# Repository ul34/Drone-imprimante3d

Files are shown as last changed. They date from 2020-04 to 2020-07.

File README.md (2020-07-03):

# Drone-imprimante3d
P.I.D &amp; I3D

                                               DRONE QUADRIMOTEUR EN X.

 Drone Frame impression 3D 

-Quel type de plastique utiliser ?

Personnellement j'ai utilisé du PETG mais cela est une solution non optimale. Le polypropylène plus difficile à imprimer, ne colle pas aux surfaces de type build-plate ou verre. Le polypropylène ne colle que sur sur le polypropylène. Son désavantage est sa résistance mécanique plus faible à l'étirement que la plupart des plastiques. Il possède néanmoins une grande résistance au choc et une bonne flexibilité. Pour notre projet la résistance au choc est essentielle.

Paramètres impression 3D 

-Surface d'impression minimale pour ce drone 180*180 mm.
-Température impression buse PETG : 245 C°
-Température impression plateau PETG : 80 C°
-Buse 0.6 mm
-Hauteur de couche 0.2 mm
Remarque: les températures d'impression varie en fonction de la marque de plastique utilisée.

Fichier impression 3D 

-Drone.montage.stl ce fichier n'est pas à imprimé, il montre juste l'assemblage des différentes piéces.
-N.basdrone.stl ce fichier contient la pièce du bas du drone avec le support de batterie (lorsque vous imprimerez cette pièce activer les supports).
-N.ruche.stl ce fichier contient la pièce du haut qui permet de fixer les bras du drone.Il faut que les losanges soient perpendiculaires au losange de la pièce du bas pour avoir une rigidité égale.
-N.bras.stl ce fichier permet d'imprimer les bras du drone, dupliquez les au nombres de 4 dans votre slicer (Cura...).
-N.calibras.stl ce fichier permet d'imprimer des pièces alignées au milieu sur la longueur et la largeur du drone. Elle permettra de glisser un rond de 6mm de diamètre pour pouvoir calibrer les coefficients P.I.D des axes PITCH et ROLL.
-N.supMPU6050.stl ce fichier contient l'impression du support gyroscope, imprimez deux support.

Matériel 

-MPU6050 *2 ~5€
-ESC 30A *4 ~20€
-arduino Uno ou arduino Mega
-Radiocommande Flysky fs-i6 avec récepteur ~45€
-Moteur brushless BR2212 1000KV *4 ~20€
-Batterie 3S 11.1v ~30€
-Hélices horaires * 2
-Hélices anti-horaires

Microcontrôleur 

L'Arduino est un circuit électronique composé d'un microcontrôleur que l'on peut appeler micro-ordinateur il possède de la mémoire morte reprogrammable (EPROM), de la mémoire vive et un processeur qui fait les calculs,il est doté d'entrée est de sortie, alors il peut communiquer de l'information sous forme électrique(OUTPUT)est recevoir de l'information(INPUT). Il ya la partie alimentation composée d'un ou de plusieurs régulateur qui va limiter la tension a 5v est 3.3v avec des Condensateur est des résistances qui permettent de stabiliser la tension, un MiCro a besoin d'une alimentation très stable pour fonctionner correctement. il y a aussi l'oscillateur qui permet au MiCro de se repérer dans le temps est déterminé aussi sa rapidité d’exécution en HZ. Puis la dernière partie qui est un convertisseur USB::UART qui vous permet de téléverser le programme dans le MiCro, mais pas que, il permet aussi de recevoir des données pour voir si notre Prog est fonctionnel. Résumons l'arduino est un MiCro "Plug&Play" qui va nous permettre de recevoir des donnés les transformer avec des calculs puis transmettre des données a des composants electronique.
Le gyroscope & accéléromètre 
-Le MPU6050 est une centrale inertielle qui réuni gyroscope et accéléromètre ce qui permet au microcontrôleur de connaître la position du drone autour de trois axe X = ROLL, Y = PITCH, Z = YAW en degrés et la vitesse a laquelle il se déplace en degrés/S. Vous verrez plus tard qu'il est paramétrable cela nous permettra de déterminer une certaines plage de mesure ou activer des filtres. Il communiquera avec l'arduino via le protocole de communication nommé "I2C".

ESC 

-Les ESC sont des circuit électronique composer d'un MiCro avec un programme qui contrôle des transistor Mosfet qui on le rôle d'interrupteur pour pouvoir commuter le courant électrique est changer le sens du champ magnétique des bobines(situées sur le stator) en fonction de la position du rotor constitué d'aimants, cette position est donnée au MiCro via des capteurs a effet Hall ou dans notre situation la force contre électromotrice. Le MiCro peut alors suivre la séquence propre au moteur et le faire tourner, pour contrôler la vitesse de rotation le MiCro utilise le rapport cyclique(PWM) en contrôlant les interrupteurs (Mosfet), pour vous donner un exemple imaginez une led avec un interrupteur que nous allumons 500ms puis éteignons 500ms et ainsi de suite nous avons alors un signal cyclique puis qu'il se répète, on peut aussi déterminer notre période qui est de 1s imaginons maintenant que notre led consomme 1 w/h = 3600 joule soit une consommation en énergie de 1 joule par seconde vu qu'une heure est égale a 3600s donc si notre led est allumée en permanence elle consomme 1 joule/S mais nous ne l'allumons que 50 % du temps donc la led recoit 50% de l'énergie quelle pourrait recevoir par apport au temps exemple sur 1h la led a consommée 1800J a la place de 3600J mais si vous faite cette expérience avec une période aussi longue 1s vous verrez la led clignoter et ce n'est pas le but recherché. L'objectif est de pouvoir moduler la luminosité de la led, pour cela il faut réduire la période pour que l'allumage et l'extinction passe sous le seuil de perception visuelle(~100ms) exemple 10ms allumé 10Ums éteint plus la période diminue plus la fréquence est élever et cela nécessite d'avoir des interrupteur qui peuvent commuter rapidement. Le calcul est le suivant (Rapport cyclique en % = durée allumé / durée période). Maintenant revenons a nos ESC plus la frequence "PWM" est élever plus la régulation de vitesse sera précise est constante, mais il faut alors un ESC avec des transistor de bonne qualité et capable de fonctionner a haute frequence pour notre premier drone se préoccuper de la frequence d'échantillonage n'a pas vraiment d’intérêt puisque nous utilisons des ESC bas de gamme. Malgré ses explication nous ne savons toujour pas comment envoyer de l'information au MiCro des ESC pour qu'il puisse réguler la vitesse mais vous allez voir que ce n'est pas très difficile, c'est notre controleur de vol qui envoie l'information au ESC, nous allons envoyer l'information en controlant la largeur d'impulsion pour étre plus clair c'est le temps que le signaux réste a l'état haut(5v) a ce niveau la frequence n'est pas trés importante pour notre cas. En général la longueur d'impulsion varie entre 1000us ce qui signifie moteur a l'arrét est 2000us qui correspond au moteur a pleine puissancece ce qui fait "théoriquement" 1000 vitesse différente possible.

- Moteur brushless

-Ce sont des moteur électrique sans balais est collecteur car ses moteur peuvent avoir une vitesse de rotation trés élever ce qui augmente la durée de vie du moteur mais il faut en contrepartie un circuit electronique pour assurer le role des balais est collecteur, l'orsque vous acheté des moteurs de drone vous verrez des inscriptions il ya d'abord les dimensions du moteur puis une indication sur la vitesse de rotation en fonction du voltage, je vais vous donner un exemple "BR2212 1000KV" vous voyez le nombre 2212, composé de quatre chifre ?. Les deux premier chiffre "22" indique le diamétre du stator et les deux suivant représente la hauteur du stator "12". Les KV vous donnent la vitesse du moteur en fonction du voltage que vous lui donné, nous avons la un moteur "1000KV" si je lui donne 2V le moteur tournera alors a 2000 tour/minutes. Nous allons maintenant parler du fonctionnement d'un moteur brushless tout d'abord il existe deux variantes le Brushless in-runner ou le stator est en périphérie est le rotor est central et le out-runner avec le stator central est le rotor appelé "cloche" a l'exterieur cela permet d'avoir un couple plus important, plus le diamétre de la cloche est important plus vous aurez de couple ces moteur sont les plus utiliser dans le monde du drone je n'ai jamais vue un moteur in-runner sur un drone. 

Le rotor se compose d'aimant permanent avec un champ magnétique fixe, le stator est composer de bobines en changant le sens du courant on inverse les poles du champ magnétique rappeller vous que le NORD attire le SUD le SUD repousse le SUD est le NORD repousse le NORD, ses la que vient la notion de séquence pour faire tourner votre moteur il va falloir alimenter les bobines en inversant le sens du courant au bon moment afin que les champs magnétiques des bobines pousse et attire dans le sens voulu les aimants permanent pour crée une rotation. Une sequence se divise en plusieurs étapes qui se répéte, pour pouvoir connaitre la position du rotor est exécuter la bonne étapes on mesure le voltage de la bobine qui n'est pas alimenté, no moteur ont trois phase donc le nombre de bobines est un multiple de trois, imaginé un moteur avec trois bobines avec un point commun a chaque étapes on alimente deux bobines sur trois est on mesure le voltage de la bobine libre cette tension varie en fonction de la position de l'aimant permanent du rotor parapport a la bobine quand l'aimant est a 180° donc alignée avec la bobine la tension est nule ses ce que l'on appelle le "ZERO CROSS" qui permet au controleur de vitesse de savoir quand passer a l'étape suivante.

- Radiocommande & recepteur

-La radiocommande vous permez de déplacer le drone autour des trois axes ROLL,PITCH,YAW est de controler les GAZ. Le récepteur qui se trouve sur le dronne recoit les signaux de la télécommande et les transmets au controleur de vol.
Le recepteur communique avec le controleur de vol via des channels et nous allons en utiliser quatre car nous avons quatre commande différente ROLL,PITCH,YAW et GAZ, la méthode de communication entre le récepteur est notre controleur de vol est la méme que celle utilisée pour controler les ESC,le recepteur enverra l'information en faisant varier la largeur d'impulsion en fonction de notre commande entre 1000us et 2000us pour lires la largeur d'impulsion soit le temps ou l'impulsion reste a l'etat haut  nous allons utiliser les interruptions de l'arduino qui s'active a chaque changement d'état.

L'orsque vous achetez votre radiocommande vous devrez choisir votre configuration de commande appeller Mode cliquez sur l'image suivante pour voir ou se trouve les commandes du PITCH,ROLL,YAW,GAZ en fonction du Mode, la deuxiéme image représente le récepteur.

- RADIOCOMMANDE

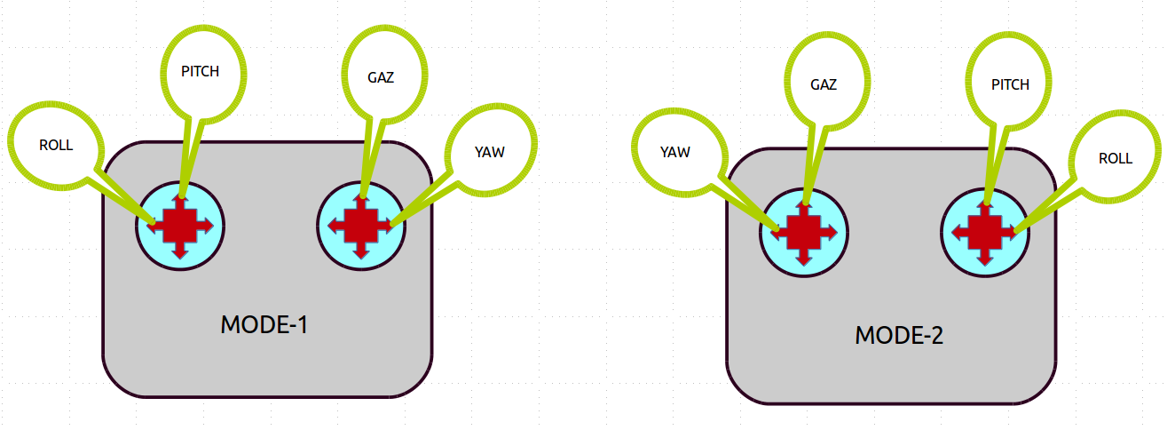
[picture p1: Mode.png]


- RECEPTEUR

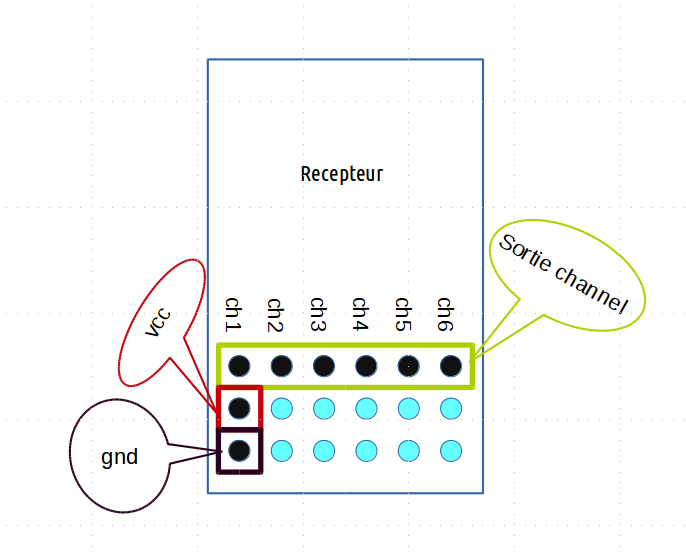
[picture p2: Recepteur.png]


- Hélices

-Les hélices permettent a notre drone de se déplacer, elle pousse l'air a une grande vitesse derriére est nous avons depuis Newton que toute masse soumise a une force (action) oppose a celle si une force égale (contre-réaction) ce qui crée la poussée. Pour choisir ses hélices il ya plusieurs caractéristiques a prendre en compte.

-Le pas géométrique

Petit pas = plus grande traction à faible vitesse, mais vitesse maxi limitée.

Grand pas = plus petite traction à faible vitesse, mais vitesse maxi élevée.

-La taille des hélices

Grande Hélice = beaucoup de portance → vol stable mais a besoin de puissance pour faire 1 tour entier → moteur important.

Petite Hélice = peu de portance → vol moins stable et à besoin de moins de puissance pour faire 1 tour entier → moteur faible.

-Nombre de pales

 nombre de pales élevés = poussée plus élevée → rendement énergétique plus faible.
 
 nombre de pales faibles = poussée plus faible → rendement énergétique élevé.
 
 Pour augmenter la poussée vous pouvez augmentez la taille des hélices mais cela a ses limites vous risquez d'arracher le rotor de votre moteur ou  de crée une usure prématuré des roulements, pour notre drone prenez des hélices de "12" pouces maximum, personnellemnt j'utilise des hélices 1045 soit "10" pouces 25cm avec un pas de 4.5.

 - Batterie & Chargeur
 
 Pour les drones on utilise des batterie lithion-ion-polymére qui on pour avantage de disposer d'une bonne densité énetgétique (Volume par unité d'energie) et la batterie est légére car elle na pas d'envellope de métal . L'orsque vous acheterez une batterie il ya plusieurs informations a prendre en compte la tension "Voltage" la capacité "mah" et le taux de décharge.
 
 -Une cellules de batterie Lipo a une tension nominale de 3.7v est maximale de 4.2v Vous verrez sur les batteries "2S,3S,4S,6S"
 notre batterie est une 3S ce qui veut dire que nous avons acheté une batterie avec 3 cellules en serie ce qui nous donnent une tension totale "11.1 = 3*3.7" et 12.6v Max. Une cellule Lipo ne doit pas decendre en dessous de 3V laisser une marge de sécurité posser votre drone a 3.5v par cellules.
 
 -La capacité de la batterie s'exprime  en ampéres/H ou plus souvent en milliampére/h sur les batteries. Si vous avez une batterie de 6000mah sa veut dire que si votre systéme consomme 6 ampéres vous aurez une autonomie d'une heure.
 
- Le capacité de decharge correspond au nombre d'ampéres maximum que l'on peut demander a notre batterie, exemple si vous avez une batterie 30C de 3000 mah vous pourrez demander a la batterie "90 = 30 *3" 90 ampéres. Un moteur consomme maximum 15AH ce qui fait "4*15 = 60" 60AH alors il faut prendre une batterie qui peut nous donner environ deux fois le courant demander soit 120AH.

-Pour charger des batterie Lipo il faut un chargeur spécial qui va equilibré les cellules entre elle et elle ne supporte pas les surcharges et le chargeur suit une procédure bien définit en debut de charge le voltage monte progressivement j'usqua atteindre 4.2v a partir de ce moment plus l'accumulateur sera remplie plus l'amperage demandé par la Batt diminue quand l'ampérage demandé descend en dessous de 3% de la capacité de votre Batt la Batt est complétement remplie. Il faut aussi dire a notre chargeur combien d'ampéres il va délivré, les batteries Lipo accepte maximum un ampérage equivalent a deux fois sa capacité "2C" cela veut dire que votre batterie sera rechargé en 30 minutes plutot rapide mais a un désavantage vous diminuer la durée de vie de votre Batt je vous conseille de recharger en "1C" soit une fois la capacité de la Batt.

 - Montage composant & soudure

  Si vous avez le matérielle nécessaire pour réaliser des circuit imprimée est vous voulez transferez le circuit sur la plaque en cuivre en utilisant de l'acetone et alcool ou en utilisant le transfert par chaleur avec un fer a repasse, imprimée avec une imprimante laser les fichiers "PCB-FC.pdf" et "PCB-power distrib.pdf". Les deux autres fichier "PCB-FC-négatif.pdf" et "PCB-power distrib-négatif.pdf" sont utile si vous faites vos circuit imprimée avec une insoleuse. Si vous n'avez pas le materielle nécessaire suivez les instructions suivante.

 -Prennez votre radiocommande brancher le cable de bind si vous avez une Flysky fs-i6 allumez la et restez appuyez sur le bouton "Bind key" cela va permettre de crée la liaison entre la radiocommande est le recepteur puis restez appuyez sur le bouton "OK" qui vous méne vers un menu avec deux sous menu "System setup" et "Functions setup" déplacer vous avec les touches "up" et "down" sur le sous menu "Functions setup" et cliquez sur "OK" puis déplacez vous sur "Display" est cliquez "OK" est la vous verrez vos channels. Bougez vos commandes est vous verrez quel commande correspond a quel channel. 
 
 Si vous avez une RaDio Mode1 vous devriez avoir le "YAW" CH1, le "PITCH" CH2, les "GAZ" CH3, le "ROLL" CH4. Maintenant nous savons quel channel du recepteur transmet quel commande. 
 
  Si vous avez une RaDio Mode2 ou autre vos commande ne seront pas assigné au méme CH dites vous que pour l'arduino uno la pin digiital 8 doit recevoir du recepteur la commande du "YAW", la pin digital 9 le "PITCH", la pin digital 10 le "ROLL", la pin digital 11 les "GAZ" et pour l'arduino mega on suis la méme logique la pin digital 53 recoit le"YAW",pin digital 52 le "PITCH",pin digital 50 les "GAZ",pin digital 10 le "ROLL". Pour finir rendez vous dans le sous menu "Functions setup" rentrez dans Reverse et inverser la CH du "YAW" et du "PITCH". Si vous vous trompez dans l'ordre des soudures ne vous embétés pas a dessouder nous verrons plus tard dans la partie programme comment changer l'assignation des pin.

    -ARDUINO UNO.
 
    le + du recpteur au +5v

    le _ du recepteur au gnd
 
    CH1"YAW" du recepteur a la pin digital 8. 

    CH2"PITCH" a la pin digital 9. 
  
    CH3"GAZ" a la pin digital 10. 
 
    CH4"ROLL" a la pin digital 11. 

    -ARDUINO MEGA PRO MINI.
 
    le + du recpteur au +5

    le _ du recepteur au gnd
 
    CH1"YAW" a la pin digital 53. 
 
    CH2"PITCH" a la pin digital 52. 
 
    CH3"GAZ" a la pin digital 50. 
 
    CH4"ROLL"  a la pin digital 10.

  passons au soudure tous dabord il faut souder un fil entre le "VCC" du MPU-2 et sa broche "ADO" puis relier le "VCC"
 des deux "MPU" sur le +3.3V de l'arduino, les deux "GND" sur un GND, les deux "SDA"(Serial data) sur "A4" les deux "SCL"(Serial clock line) sur "A5". Pour plus de solidité est éviter l'arrachement d'un fils réunissez les et faite une trésse.

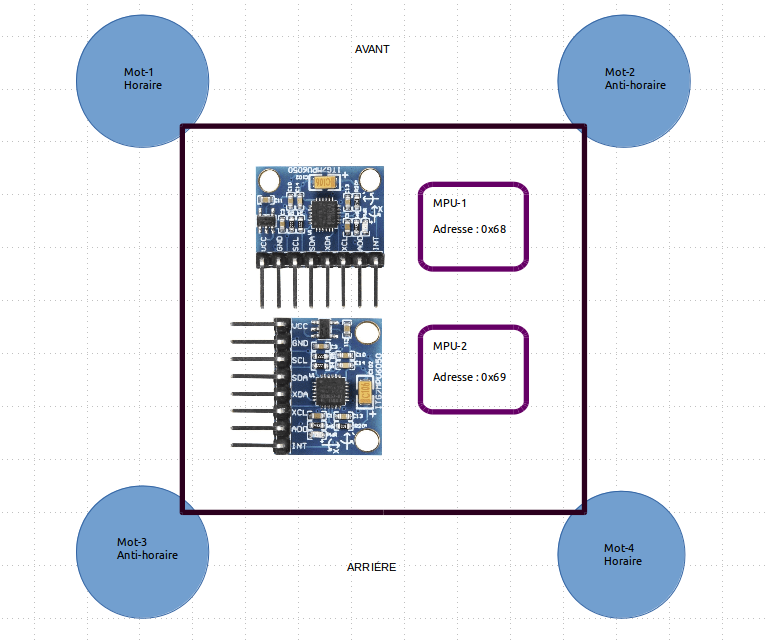
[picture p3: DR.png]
  

  -Il reste alors les ESC a installée est a racorder a l'arduino, regarder l'image ci-dessous est vous verrez les deux fils d'alimentation (+12v,-) le fils signaux avec son gnd puis les trois fils moteur, rappeller vous nos moteur on trois phases et tous les moteurs de notre drone ne tourne pas dans le méme sens regarder de nouveau l'image ou il ya les deux gyroscopes vous verrez quel moteur tourne dans quel sens, horaire ou anti-horaire. Pour inverser le sens d'un moteur il suffit d'inverser le branchement des fils moteur. Maintenant nous allons souder aux arduino les fils du signaux de chaque ESC . 
  
    -ARDUINO UNO.
  
    ESC.moteur1 a la pin digital 4 
  
    ESC.moteur2 a la pin digital 5 
  
    ESC.moteur3 a la pin digital 6 
  
    ESC.moteur4 a la pin digital 7  
  
    -ARDUINO MEGA PRO MINI.  
  
    le ESC.moteur1 a la pin digital 26 
  
    le ESC.moteur2 a la pindigital 27 
  
    le ESC.moteur3 a la pin 28 
  
    le ESC.moteur4 a la pin 29 
  
    Reliez tous les gnd des signaux au gnd de l'arduino.
  
Pour alimenter les quatre ESC il faut fabriquer une "Power distribution board" on va faire un circuit imprimée comme sur l'image ci-dessous, prenez votre plaque de cuivre est un marqueur indélébile est redessiner les partie en rouge puis tremper la plaque de cuivre dans une solution de perchlorure de fer est agiter doucement il devrait rester que les parties colorier, les deux rectangle et le diviseurs de tension , mes a quoi le diviseur de tension peut il  servir ? l'arduino ne peut mesurer que des tensions inferieur ou égale a 5v notre batterie fait 12.6v pour pouvoir mesurer le niveau de charge de notre batterie et compenser la puissance des moteurs quand le voltage diminue, pour éviter d'avoir des commandes de moins en moin réactive au fils du vol il faut que l'arduino puisse mesurer le voltage alors nous méttons une diode avec deux resistances en serie est nous soudons un fil entre les deux resistances que nous relions a la pin analogique 0 . 

Et voici le calcul qui nous permet de connaitre la valeur de "R1 = (U/U2)*R2-R2"  je choisi une valeur de resistance arbitraire pour R2 elle doit tous de méme étre assez élever pour que notre circuit ne consomme pas trop de courant (I = U/R) on va prendre une valeur de 1000 Ohm, U represente la valeur de notre alimentation "12.6v", U2 la tension que l'on veut entre R1 et R2 donc 5v "R1=1520 =(12.6/5)*1000-1000" donc pour que U2 ou la broche Analogique 0 soit a 5v quand la batterie est a sa tention maximale il faut que R1 soit égale a 1520 Ohm, nous mettons une Resistance de 1.5k les 20 Ohm supplementaire n'ont pas un effet significatif et R2 1000 Ohm. Pour que votre dronne vous previennent l'orsque votre batterie est décharger branchez un "Buzzer" sur la pin digitale 13.

Conseil: l'orsque vous souderé la power distribution n'hésitez pas a mettre une couche d'etein sur les pistes avec les huit trous pour alimenter vos ESC il peut passer dans ces pistes un courant de 60 amperes et risque de crée une surchauffe.

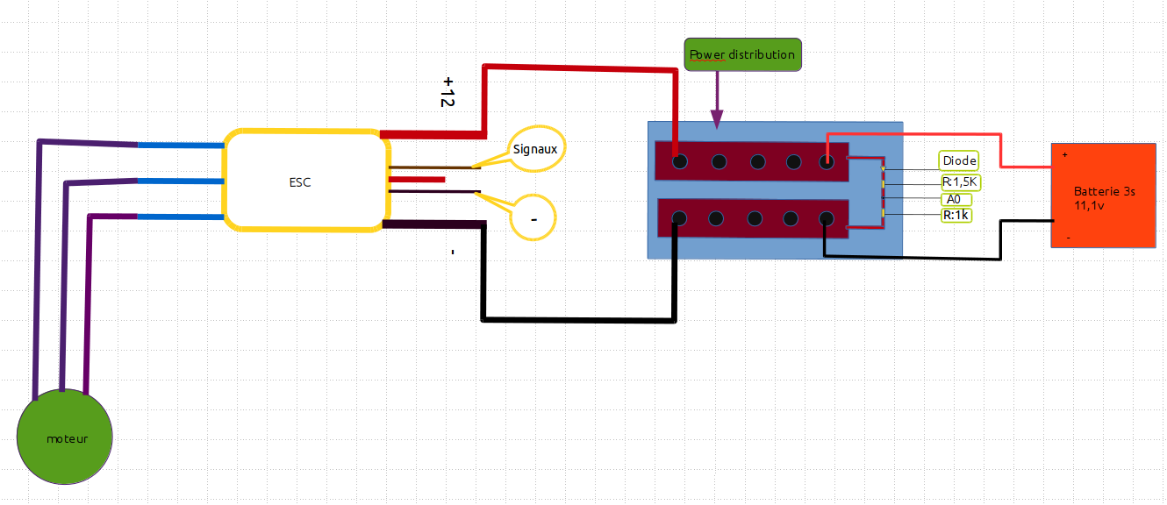
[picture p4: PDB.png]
 

   L'orsque vous monté votre Drone découpé des piéces  en chambre a air ou des pads en silicone pour les mettres entre les moteurs et les bras ne séré pas trop vos moteurs car le pouvoir enti vibrant sera limité, rajouté des piéces en chambre a air entre les bras des moteurs est les deux plaques qui les jointes sa permettra de limiter les vibrations et d'éviter au bras de bouger. Si vous placer votre arduino ou le Circuit imprimé entre les deux plaques placer le port USB de l'arduino prés des bords pour pouvoir téleverser les programmes. Mettez aussi du frein a filer sur les tiges filetés qui fixe les moteurs.

 - Programme
 
 -Le fichier "ESCALIB.ino" va nous permettre de calibrer les ESC , une fois le programme televerser ouvré le Serial  taper "1" puis "Entrée", branchez la batterie puis taper "0" la vous entendrez trois "beep" cela signifie que votre batterie est une 3S pour finir rentrer "2" dans le Serial, vous verrez vos moteur montez en puissance jusqu'a leur puissance maximale puis ils éteignent . Si vous avez l'aruino mega pro mini il faut changer la declarations des pin en mode OUTPUT "DDRD |= B11110000;" en  "DDRA  |= B11110000;" et changer toutes l'activation des pins a l'état haut "PORTD |= mot;" en "PORTA |= mot;" et a l'etat bas 
 "PORTD &=  B00000000;" en "PORTA &=  B00000000;".

 Que fait notre programme ESCALIB.ino ?
 
 L'orsque vous rentrez  "1" l'arduino envoie au ESC  chaque 8ms une impulsion de 2000us qui est la valeur maximaxe ce qui va mettre l'ESC en mode programmation puis quand on rentre "0" l'arduino envoie des impulsions de 1000us ce qui indique au ESC quel largeur d'impulsion est égale au moteur eteint, donc 2000us est égale a la vitesse maximale et 1000us au moteur eteint. Puis quand on rentre "2" on incremente une valeur a l'impulsion minimale j'usqu'a ateindre sa valeur maximale puis on retourne a une l'argeur d'impulsion de 1000us. 

 -Maintenant que nous avons nos ESC calibré rendez vous sur ce lien https://github.com/jrowberg/i2cdevlib est télécharger les fichier, dans tous ces fichier il ya deux bibliothéque qui nous intéresse "I2Cdev.h" et MPU6050.h une fois que vous les avez intégré les dans votre IDE, télecharger le programme ecrit par Luis RODENA qui se trouve dans le fichier "...." qui va nous permettre de calibrer nos deux Gyro. 

 Pour le faire il faut d'abord bien positionner votre drone a plat en  utilisent un niveau a bulle, une fois qu'il est bien a plat on va pouvoir televerser le programme dans notre arduino. Mais nous avons deux Gyro a calibrer nous allons les calibrer un a la fois pour savoir lequel des deux nous sommes entrein de calibrer il faut connaitre l'adresse de chaque Gyro notre MPU-1 a pour adresse "0x68" et MPU-2 "0x69". Regarder le programme vous verrez cette ligne "MPU6050 accelgyro(0x69);" pour pouvoir changer de Gyro il suffit de changer l'adresse qui est entre parenthése par l'adrresse de votre Gyro.

 Une fois que vous avez choisi l'adresse téleverser le programme, pour le lancer ouvré le Serial  est rentré un caractére au hasard aprés une trentaine de seconde vous verrez apparaitre une ligne avec ecrit "Sensor readings with offsets" suivie de six nombre qui doivent etre proche de la suite suivante "0 0 16384 0 0 0",la ligne suivante ou il ya ecrit "Your offsets" suivie de six nombre "-3771 -1100 1106 -10 70 -8" se sont vos valeurs de calibration pour les trois axes de l'accelerométre est les trois axes du gyroscopes. Faites cette opération pour les deux Gyro puis ouvrez le fichier "...." si vous utilisez l'arduin uno ou "...." pour l'arduino mega pro mini est remplacer les six valeurs suivante pour chaque Gyro par vos valeurs d'offset.  

    mpu.initialize(); //MPU-1 = 0x68
  
    mpu.setXAccelOffset(-3771);
  
    mpu.setYAccelOffset(-1100);
 
    mpu.setZAccelOffset(1106);
  
    mpu.setXGyroOffset(-10);
  
    mpu.setYGyroOffset(70);
  
    mpu.setZGyroOffset(-8);
  
    mpu1.initialize(); //MPU-2 = 0x69
  
    mpu1.setXAccelOffset(497);
  
    mpu1.setYAccelOffset(1703);
  
    mpu1.setZAccelOffset(1148);
  
    mpu1.setXGyroOffset(-629);
  
    mpu1.setYGyroOffset(206);
  
    mpu1.setZGyroOffset(-8);

  Normalement apres avoir televerser le programme "FCuno.ino" votre dronne est prét a voler. Pour eviter les accidents il faut faire une combinaison de mouvement avec les stick pour allumer les moteurs et que votre drone soit prét a décoller ou une autre combinaison pour eteindre les moteurs.
  
  -Décollage

  -Eteindre

  Conseil: Pour vous assurez que tous fonctionnent bien ou changer les coefficient PID faite un banc de test. Imprimée quatre piéces du fichier "N.calibras.stl" et coller les au millieux sur les cotés du drone et aligné bien les piéces pour pouvoir passer un rond de 6mm. Puis faites un cadre ou trouver deux endrois ou fixer les deux bouts du rond.

  - Explication Programme
  
  Notre programme recoit les commandes ordonné par notre radiocommande qui lui donne un angle a atteindre (Consigne) est les donnés du gyroscopes qui lui donne sa position actuelle est a la vitesse a laquelle le drone se déplace autour de ses trois axes,pour que le drone suive la consigne quon lui donne nous allons utiliser un régulateur P.I.D qui en fonction de la vitesse de déplacement du drone de sa position et de la consigne va distribuer la puissance des moteurs pour atteindre la consigne et se stabiliser.

  -lecture des données recus par le recepteur

  Pour calculer l'angle a atteindre il faut d'abord lire la largeur d'impulsion de chaque CH rappeller vous on en a parler dans la partie " Radiocommande & recepteur" pour lire la largeur on va utiliser les interruptions en mode "Changes" ce qui veut dire quells activent l'orsque l'état de la CH passent de l'etat haut(5v) a bas(0v) ou de bas a haut.  Quand une interruption s'activent elle est prioritaire sur notre programme et lance une routine execution qui va faire les calculs pour connaitre la largeur d'impulsion. Une fois que le code de la routine est executer le programme reprend ou il ces arrété, si le code de la routine est trop volumineux votre programme ne fonctionnera pas car elle sera réappeller alors que l'execution du code n'est toujour pas finit.

Pour pouvoir les utiliser il faut declarer les interruptions le code suivant indique a l'arduino uno que les pins digital 8,9,10,11  vons etre uitliser comme interruptions en modes "Changes".  
   
     //N°bit = 76543210   //table de vérité "ou" = "1&0=1" "0&0=0" "1&1=1 

    //PCIRC = 00000000;

    //PCMSK0 = 00000000;

    PCICR  |= (1 << PCIE0); //PCIRC = 00000001; on met le bit 0 du registre PCICR a 1 

    PCMSK0 |= (1 << PCINT0); //PCMSK0 = 00000001; on met le bit 0 du registre PCMSK0 a 1 Pin digital 8

    PCMSK0 |= (1 << PCINT1); //PCMSK0 = 00000011; on met le bit 1 du registre PCMSK0 a 1 Pin digital 9

    PCMSK0 |= (1 << PCINT2); //PCMSK0 = 00000111; on met le bit 2 du registre PCMSK0 a 1 Pin digital 10

    PCMSK0 |= (1 << PCINT3); //PCMSK0 = 00001111; on met le bit 3 du registre PCMSK0 a 1 Pin digital 11

Pour bien comprendre le fonctionnement il faut imaginer un octet superposer a un autre octet ces pour sa que le "ou" est un comparateur de bit je vais donner des exemples

    PCMSK0 = 00000000; // le registre PCMSK0 se représente sur un octet 

    l'orsque nous faisons |= (1 << PCINT0) il se passe la chose suivante nous créons un octet et nous faisons se décaler vers la     gauche la valeur 1 de 0 bit "00000001" et on compare notre octet a l'octet du registre PCMSK0.

    PCMSK0 = 00000000;

                 |=          PCMSK0 =  00000001;

            00000001;
     
    l'orsque nous faisons |= (1 << PCINT1) il se passe la chose suivante nous créons un octet et nous faisons se décaler vers la     gauche la valeur 1 de 1 bit "00000010" et on compare notre octet a l'octet du registre PCMSK0.

    PCMSK0 = 00000001;

                 |=          PCMSK0 =  00000011

             00000010;

Maintenant que nous avons déclarée nos interruptions au pins 8,9,10,11 nous pouvons allez dans notre routine d'execution et taper notre code pour calculer la largeur d'impulsion.

     ISR(PCINT0_vect) //routine execution qui s'activent a chaque changement d'etat
     {
    current_time = micros(); // on lance un timer et on stoke T0

    if (PINB & B00000001) {  // SI pin digital 8 est a l'etat haut on execute le code entre les accolades                                       
        if (previous_state[0] == LOW) { // Si la variable previous_state[0] est égale a LOW                 
            previous_state[0] = HIGH;  // previous_state[0] est égale a HIGH                      
            timer[0]          = current_time; // on stoke T0 dans  timer[0]              
        }
    } else if(previous_state[0] == HIGH) { // SI pin 8 a l'etat bas et que previous_state[0]==HIGH              
        previous_state[0] = LOW;  // previous_state[0] est égale a LOW                              
        pulse_duration[0] = current_time - timer[0]; Durée a l'état haut T1-T0 
    }
    }
    
 Pour bien comprendre imaginés que la pin D8 est a l'état bas(LOW) quand on allume le drone la pin D8 passe a l'état haut alors la routine d'execution s'activent on stoke dans la variable "current_time" le temps actuelle prenont une valeur arbitraire a titre d'exemple "current_time = 1000us" aprés nous testons une condition Si pin D8 est a l'etat haut on execute le code entre les accolades dans ces accolades il ya un autre test de condition Si la variable "previous_state[0]" est a l'etat bas et elle les car nous venons juste d'allumer l'arduino est la variable est initialiser a 0 soit etat bas on passe alors "previous_state[0]" a l'etat haut et on stoke le temps actuelle dans timer[0] soit 1000us,  le prochain test de condition "else if(previous_state[0] == HIGH)" est faux et n'execute pas le code entre les accollades car les test de condition est fault car "if (PINB & B00000001)" est vrai. Puis nous sortons de la routine d'exe est l'arduino recommence a executer le code la ou il c'était arrété. L'orsque la pin D8 change d'etat a nouveau sa veut dire pour nous quel va passer de l'état haut a l'etat bas la routine exe se relance on stoke comme a chaque nouvelle rentré dans la routine le temps actuelle dans "current_time = 2500us" cette fois si la condition "if (PINB & B00000001)" est fausse donc le code entre les accolades ne s'execute pas mais la condition "else if(previous_state[0] == HIGH)" est vrai car la premiere condition est fausse est "previous_state[0]" avais été mis a l'etat haut "HIGH" alors on execute le code entre accolades on repasse  "previous_state[0]" a l'etat bas "LOW" est ont soustrait le temps stoker dans "timer[0] = 1000us" l'or de la premiére activation de la routine au temps actuelle soit "current_time = 1500us" ce qui fait "pulse_duration[0] = 2500-1000;", maintenant nous pouvons connaitre la largeur d'impulsion de chaque CH ROLL, PITCH, YAW, GAZ.

 Rappelez vous notre recepteur envoie a notre controleur de vol des largeurs d'impulsion entre 1000us et 2000us l'orsque vous ne touchez pas les commandes du PITCH, ROLL, YAW de votre radiocommande la largeur d'impulsion est de 1500us ce qui veut dire que vous demandez a votre drone d'étre a plat "PITCH = 0°, ROLL = 0°, YAW = 0°/S" pour les GAZ 1000us signifie GAZ = minimum et 2000 us GAZ = maximum. Maintenant nous allons voir le code qui permet de transformez les largeurs d'impulsions en consigne.

     void consigne(){
  
           ConsG = 0; // A chaque boucle du programme on met la variable ConsG = "GAZ" a 0
          ConsP = 0;  // A chaque boucle du programme on met la variable  ConsP = "PITCH" a 0
          ConsR = 0; // A chaque boucle du programme on met la variable  ConsR = "ROLL" a 0
         ConsY = 0; //  // A chaque boucle du programme on met la variable  ConsY = "YAW" a 0
  
    chanel1 =  pulse_duration[2]; // on stoke la largeur d'impulsion CH "GAZ" dans la variable chanel1 
    chanel2 =  pulse_duration[1]; // on stoke la largeur d'impulsion CH "PITCH" dans la variable chanel2 
    chanel3 =  pulse_duration[3]; // on stoke la largeur d'impulsion CH "ROLL" dans la variable chanel3 
    chanel4 =  pulse_duration[0]; // on stoke la largeur d'impulsion CH "YAW" dans la variable chanel4
  
    if (chanel1 < 1000) chanel1 = 1000; // on limite les valeurs entre 1000 et 2000
     if (chanel1 > 1800) chanel1 = 1800;
     if (chanel2 < 1000) chanel2 = 1000;
     if (chanel2 > 2000) chanel2 = 2000;
    if (chanel3 < 1000) chanel3 = 1000;
    if (chanel3 > 2000) chanel3 = 2000;
    if (chanel4 < 1000) chanel4 = 1000;
    if (chanel4 > 2000) chanel4 = 2000;

  Maintenant qu'on a stoké les valeurs du "PITCH, ROLL, YAW, GAZ" est qu'on a limité les valeurs dans un intervalle [1000;2000]  on va séparé les intervalles en deux parties " ROLL = [1000<=gauche<1500>droite<=2000], PITCH = [1000<=avant<1500>arriére<=2000] , YAW = [1000<=droite<1500>gauche<=2000] pour les GAZ nous n'avons pas besoins de separer en deux l'intervalle. Comme le signal a du bruit il n'est pas parfaitement constant a 1500 ces pour ca que nous laisons une marge de 16us.

    //gaz
    if (chanel1 >1008){ // Si strictement plus grand que 10008 allumage des moteurs
    ConsG = chanel1;
     }

    //Pitch
    if (chanel2 >1508){ // SI strictement plus grand que 1508 "PITCH" vers l'arriére arriére
     ConsP = (chanel2-1508);
     }else if (chanel2 < 1492){ //sinon SI strictement plus petit que 1492 "PITCH" vers l'avant
     ConsP = (chanel2-1492);
     }
    
      //Roll
    if (chanel3 >1508){ // SI strictement plus grand que 1508 "ROLL" vers la droite 
     ConsR = (chanel3-1508);
     }else if (chanel3 < 1492){ //sinon SI strictement plus petit que 1492 "ROLL" vers la gauche
     ConsR = (chanel3-1492);
     }
     
       //Yaw
    if (chanel4 >1508){ // SI strictement plus grand que 1508 "YAW" vers la  gauche 
     ConsY = (chanel4-1508);
     }else if (chanel4 < 1492){  //sinon SI strictement plus petit que 1492 "YAW" vers la droite
     ConsY = (chanel4-1492);
     }

   Si sur votre radiocommande vous poussez le stick du Roll sur la droite et que la largeur d'impulsion dépassent 1508, on soustrait 1508 a la valeur recu ce qui nous donne une  Consigne qu'il faut convertir en angle a atteindre et nous savons que la largeur d'impulsion et au maximum 2000us il faut alors definir quel angle correspond a 2000us sa sera l'inclinaison maximale du drone.  Imaginez maintenant que vous poussez le stick du ROLL a droite en bout de course "chanel3 = 2000" ce qui fait      "ConsR = 2000-1508 = 492" est nous voulons que cette valeur représente 30.75° alors il faut que quand notre gyroscope indique 30.75°, ConsR soit égale a 0 alors si notre drone a une inclinaison de 30.75° il faut que l'angle soit multiplier par un coefficient et que le produit de cette multiplication soit égale a 492. Voici le calcul "492/Anglemax = coefficient"  si dessous vous avez un exemple les variables anglemaxP et  anglemaxR   stocke le  produit des multiplication entre les coefficients est l'angle actuelle pour l'axe du "ROLL" et du "PITCH" puis on soustrait les produit aux consigne et enfin on divise par trois pour limiter la vitesse de déplacement autour des axes a 164 °/S "492/3 = 164". Pour l'axe du "YAW" on ne fixe pas d'angle maximale mes une vitesse de deplacement maximale. 

     anglemaxP = 16 * angleP; // 2000-1508 = 492 , 492/16 = 30.75°, 492/30.75 = 16
     anglemaxR = 16 * angleR;
      
      ConsP -= anglemaxP ;
      ConsP /= 3;  // limitation de la vitesse de deplacement a 164°/S "492/3=164"
      ConsR -=  anglemaxR;
      ConsR /= 3;
      ConsY /= 3;

 Maintenat que nous avons les consignes de nos trois axes nous allons utiliser un régulateur P.I.D pour controler la position du drone mais d'abord je vais vous expliquer le fonctionnement de ce régulateur.
 
   le régulateur P.I.D va calculer les erreurs Proportionnelle.intégrale.Dérivée entre les Consignes et les mesures du Gyro pour chaque axe, et ont multiplie chaque erreurs par un coefficient puis on fait la sommme des trois erreurs qui sera notre commande a envoyer au moteur, chaque erreur na pas les mémes effets sur notre systéme.
 
 -L'erreur Proportionnelle correspond a l'écart entre la valeur mesurée et notre Consigne, cette ecart est multiplié par un coefficient plus il est grand plus votre systéme atteindra sont objectif rapidement mais un coeff trop grand crée des oscillations qui destabilise votre systéme, un coeff trop petit ne nous permettra pas d'atteindre l'objectif il faut alors trouver un bon compromis entre la vitesse pour atteindre l'objectif et de trop grand dépassement. Si nous utilisons seulement l'erreur proportionnelle le systéme oscilleré et n'arriverais pas a se stabiliser dans le temps sur l'objectif(Erreur statique).
 
 -L'erreur intégrale fait la somme des erreurs Prop au fil du temps cette erreur est complementaire a l'erreur Prop elle permet de reduire l'erreur statique dans le systéme si le coeff de l'erreur intégrale est trop élever cela crée  des oscillation est des grands dépassement de la consigne si il est trop faible votre systeme derivera est ne maintiendra pas l'objectif.
 
 -L'erreur dérivé, soustrai l'erreur Prop précédente a l'erreur Prop actuelle elle permet a notre systéme d'anticiper les déplacements donc dévité les dépassements de consigne si votre coeff dérivé est trop élevé vous verrez votre systéme oscillé a haute fréquence si il est trop bas il y aura des dépassements de consigne important.
 
 Si vous voulez voir les differents effets des coefficiens des erreurs "Prop,Int,Dev" regardez cette video :https://www.youtube.com/watch?v=uXnDwojRb1g.
 
 Sur votre banc de test faite varier les coefficients en fonction de vos préférence.

     float KYP = 6; // Coefficient Erreur Prop "YAW"
     float KYI = 0.22; // Coefficient Erreur intégrale "YAW"
     float KYD = 0; // Coefficient Erreur dérivé "YAW"

     float KRP = 1.3; // Coefficient Erreur Prop "ROLL"
      float KRI = 0.04; // Coefficient Erreur integrale "ROLL"
      float KRD = 18; // Coefficient Erreur dérivé "ROLL"

     float KPP = 1.3; // Coefficient Erreur Prop "PITCH" 
      float KPI =0.04; // Coefficient Erreur intégrale "PITCH"   
     float KPD = 18; // Coefficient Erreur derivé "PITCH"
 
     void PID(){

      EpropP = ASP - ConsP; //erreur proportionnelle "PITCH"
      EpropR = ASR - ConsR; //erreur proportionnelle "ROLL"
      EpropY = ASY - ConsY; //erreur proportionnelle "YAW"

      EintP +=  EpropP; //erreur intégrale "PITCH"
      EintR +=  EpropR; //erreur intégrale "ROLL" 
      EintY +=  EpropY; //erreur intégrale "YAW"
 
     if ( EintP > 400 ) EintP = 400; // on limite les valeurs de l'intégrale pour éviter d'avoir des valeurs disproportionner                                                              
     if ( EintP < -400 )EintP = -400;   qui engendrerées des dépassement effet "WindUp"
     if ( EintR > 400 ) EintR = 400;
     if ( EintR < -400 )EintR = -400;
     if ( EintY > 400 ) EintY = 400;
     if ( EintY < -400 )EintY = -400;

     EdevP =  EpropP-lastEP;  //erreur derivée "PITCH"
     EdevR =  EpropR-lastER; //erreur derivée "ROLL"
     EdevY =  EpropY-lastEY; //erreur derivée "YAW"

     lastEP =  EpropP; // On stoke l'erreur précédente du "PITCH"
     lastER =  EpropR; // On stoke l'erreur précédente du "ROLL"
     lastEY =  EpropY; // On stoke l'erreur précédente du "YAW"

    EPIDR = KRP * EpropR + KRI * EintR + KRD * EdevR; // Somme des erreurs pour l'axe du "ROLL"
    EPIDP = KPP * EpropP + KPI * EintP + KPD * EdevP; // Somme des erreurs pour l'axe du "PITCH"
    EPIDY = KYP * EpropY + KYI * EintY + KYD * EdevY; // Somme des erreurs pour l'axe du "YAW"

     if ( EPIDP > 400 ) EPIDP = 400; // on limite les valeurs de sortie pour quel reste coherente avec les valeurs que l'on 
     if ( EPIDP < -400 )EPIDP = -400;   enverra au moteur
     if (EPIDR > 400 ) EPIDR = 400;
     if (EPIDR < -400 )EPIDR = -400;
     if ( EPIDY > 400 ) EPIDY = 400;
     if ( EPIDY < -400 )EPIDY = -400;
 
    }

Maintenant on va voir la partie du code qui va nous permettre de calculer les valeurs que l'on va envoyer aux ESC de chaque moteur en fonction des sorties du régulateur PID .
     
     void Signeauxcorrec(){
       if ( decollage == 1){ 
     mot1 = ConsG-EPIDR-EPIDP-EPIDY;
     mot2 = ConsG+EPIDR-EPIDP+EPIDY;
     mot3 = ConsG-EPIDR+EPIDP+EPIDY;
     mot4 = ConsG+EPIDR+EPIDP-EPIDY;
     }

 On rajoute la consigne GAZ a tous les moteur et nous soustrayons ou additionnons les sorties du controleur PID en fonction du signe de ses sorties, pour comprendre le mieux est de voir des exemples.
 
 Imagines votre drone qui se deplace autour de l'axe du "PITCH" vers l'avant a une vitesse de -10°/S est que votre Consigne est   égale a 0 donc votre programme doit monter la puissance des deux moteur a l'avant "mot1, mot2" et baisser la puisssance des moteurs arriéres "mot3, mot4". Le regulateur PID fait ce calcul "EpropP =-10-0" la valeur de sortie et négative -10 alors il faut que l'orsque j'ajoute -10 au "mot1, mot2" la valeur doit étre positive + 10 et restez négative pour "mot3, mot4", pour que sa soit positif il suffit de mettre - car "0--10" = +10 est mettez + pour que la valeur se soustrai "0+-10 = -10".
 
    Exemple Détaillé.
 
      KPP = 1;      // Contexte : Pitch = -2°, Pitch = -10°/S, Consigne Pitch = 0°
      KPI = 1;
      KPD = 1
 
    anglemaxP = 16 * angleP; // -32 = 16*-2;
    ConsP -= anglemaxP ; // 32 = 0--32;
    EpropP = ASP - ConsP; // -42 = -10-32;
    EintP +=  EpropP; // -42 = 0 + -42;
    EdevP =  EpropP-lastEP;  -42 - 0;
    EPIDP = KPP * EpropP + KPI * EintP + KPD * EdevP; // -126 = 1 * -42 + 1 * -42 + 1 * -42;
  
     mot1 = ConsG-EPIDR-EPIDP-EPIDY; //1326 = 1200 - 0 --126 - 0;
     mot2 = ConsG+EPIDR-EPIDP+EPIDY; // 1326 = 1200 + 0 --126 + 0; 
     mot3 = ConsG-EPIDR+EPIDP+EPIDY; // 1074 = 1200 - 0 +-126 + 0;
     mot4 = ConsG+EPIDR+EPIDP-EPIDY; // 1074 = 1200 + 0 +-126 - 0;

 Si a l'inverse le drone se deplace autour de l'axe du "PITCH" vers l'arriére  a une vitesse de 10°/S est que votre Consigne est   égale a 0, il faut alors baissé la puissance de "mot1, mot2" est augmentez la puissance de "mot3, mot4". "EpropP =10-0" la valeur de sortie est positive +10 pour le "mot1, mot2" sa fait "0-+10 = -10" et pour "mot3, mot4" sa fait "0++10= +10.

    Exemple Détaillé.
 
    KPP = 1;         // Contexte : Pitch = 2°, Pitch = 10°/S, Consigne Pitch = 0°
    KPI = 1;
    KPD = 1
 
     anglemaxP = 16 * angleP; // 32 = 16*2;
    ConsP -= anglemaxP ; // -32 = 0-32;
    EpropP = ASP - ConsP; // 42 = 10--32;
    EintP +=  EpropP; // 42 = 0 + 42;
    EdevP =  EpropP-lastEP;  42 - 0;
    EPIDP = KPP * EpropP + KPI * EintP + KPD * EdevP; // 126 = 1 * 42 + 1 * 42 + 1 * 42;
  
     mot1 = ConsG-EPIDR-EPIDP-EPIDY; //1074 = 1200 - 0 -126 - 0;
    mot2 = ConsG+EPIDR-EPIDP+EPIDY; // 1074 = 1200 + 0 -126 + 0; 
    mot3 = ConsG-EPIDR+EPIDP+EPIDY; // 1326 = 1200 - 0 +126 + 0;
    mot4 = ConsG+EPIDR+EPIDP-EPIDY; // 1326 = 1200 + 0 +126 - 0;

 La prochaine partie va mesurée le voltage de la batterie et ajuster la puissance de chaque moteur et limiter les valeurs pour quel soit cohérente avec nos ESC,vous pouvez régler la valeur limite basse de vos moteurs cette valeur c'est la vitesse de vos moteur quand vos GAZ seront a zero si vous la montez un peut est que vous mettez les gaz en position zero votre dronne retombera moins vite si vous l'augmentez trop votre drone decollera alors que vous n'avez pas touché les GAZ . Si la batterie est en dessous de 3.3v par cellules le buzzer s'activent.

     void Signeauxcorrec(){
    if ( decollage == 1){ // L'orsque le decollage est activé  
    
    //on mesure le voltage de la batterie et on filtre le signal
    batterieV = batterieV * 0.92 + (analogRead(0) + 65) * 0.09853; 
   
    // on incrémente les valeurs au moteur en fonction du voltage
    if ( batterieV < 1240 &&  batterieV > 800){  
     mot1 += mot1 * ((1240 - batterieV)/(float)3500);
     mot2 += mot2 * ((1240 - batterieV)/(float)3500);
     mot3 += mot3 * ((1240 - batterieV)/(float)3500);
    mot4 += mot4 * ((1240 - batterieV)/(float)3500);
    }
    
    //on active le buzzer Si le voltage de la batterie est plus petit que 10V
     if ( batterieV < 1000 ){  
     digitalWrite(13,HIGH);
     
     }else{
       digitalWrite(13,LOW);
     }

     // on limite les valeurs de chaque moteur quand
     if (mot1 < 1100) mot1 = 1050; // valeur basse
     if (mot1 > 2000) mot1 = 2000; // valeur haute
     if (mot2 < 1100) mot2 = 1050;
     if (mot2 > 2000) mot2 = 2000;
     if (mot3 < 1100) mot3 = 1050;
     if (mot3 > 2000) mot3 = 2000;
     if (mot4 < 1100) mot4 = 1050;
     if (mot4 > 2000) mot4 = 2000;
  
    } else{ // valeur a l'arret
    mot1 = 1000;
    mot2 = 1000;
    mot3 = 1000;
    mot4 = 1000;
    }
    }

Vous avez surement vue la variable "decollage" mais je ne vous et pas dit a quoi elle pouvée servir. Elle permet d'éviter les démarges intempéstif des moteurs si par accident vous tomber votre radiocommande. Pour que vos moteur démarre et que votre drone sot prét a décoller il faut faire une combinaison de mouvement de stick, pareil si vous voulez eteindre les moteurs du drone il faut faire une autre combinaison. La partie de code suivante va tester les CH pour connaitre nos mouvement de stick et mettre la variable décollage a 1 "moteur allumer prét a decollé" ou decollage a 0 "moteur a "l'arret".

     void activation(){
     // Si les conditions sont vraie change la variable decollage est on appelle la fonction resetvariable()
    if(decollage == 0 && chanel1 <= 1008 && chanel4 > 1980 && chanel3 > 1980){ 
    decollage = 1; 
    resetvariable(); // On met les variables du regulateur PID a 0 
    } 
    // Si les conditions sont vraie on change la variable decollage
    if(decollage == 1 && chanel1 <= 1008 && chanel2 > 1980 && chanel4 < 1008){
    decollage = 0;
    } 
 
    }

  Nous allons voir le code qui va envoyer au ESC l'impulsion entre [1000us & 2000us] il va aussi fixer la frequence du programme a 250 Hz.

    void transmission(){

    while (micros()-prevmicros < 4000); // si notre boucle a pris moins de 4ms on attend.
    
    prevmicros = micros(); //on stocke le temps écoulé
     PORTD |= B11110000; // On met a l'etat haut les pins digitales 4,5,6,7,8

    while( PORTD >= 16){ // Si l'une des pins est a l'etat haut on boucle 
    prelmicros = micros(); // on stocke le temps écoulé
    if ( (mot1 + prevmicros) <= prelmicros) PORTD &= B11101111;
    if ( (mot2 + prevmicros) <= prelmicros) PORTD &= B11011111;
    if ( (mot3 + prevmicros) <= prelmicros) PORTD &= B10111111;
    if ( (mot4 + prevmicros) <= prelmicros) PORTD &= B01111111;
  
    }
  
    }
    
 Dans cette petite partie du programme on met toute les broches des ESC a l'etat haut puis on boucle temps que toute les pins sont a l'etat haut. Dans la fonction while on rajoute au temps stocké dans la variable "prevmicros" les valeurs de nos moteurs puis on met les broches a l'etat bas une fois que le temps actuelle stocké dans "prelmicros" et égale ou dépasse "mot+prevmicros", une fois que toute les broches sont a l'état bas "PORTD = 00001111" ce qui vaut 15 en décimal alors on sort de la boucle du while().

   Nous allons voir le code qui permet de configurer le deux gyroscopes et accélérométres. Récupéré les données brute et les transformés en angle° et en angle°/S.

        #include <Wire.h>
   
      void communication(){
  
     Wire.beginTransmission(MPU_ADDRESS); //  on envoie l'adresse 0x68 au MPU-1 (Slave) pour lancer la transmission
     Wire.write(0x6B);// on ecrit un octet qu'on place en attente pour communiquer avec le registre PWR_MGMT_1
     Wire.write(0x00);// on ecrit un octet qu'on place en attente pour configurer la clock 8Mhz et l'alimentation
     Wire.endTransmission(); // on evoie les octets mis en attente et on termine le transmission

      Wire.beginTransmission(MPU_ADDRESS); // on envoie l'adresse 0x68 au MPU-1 (Slave) pour lancer la transmission 
      Wire.write(0x1B);// ..................... pour communiquer avec le registre GYRO_CONFIG  
      Wire.write(0x08);//........... on configure le plage de mesure du gyroscope 0°/S a ±500°/s
      Wire.endTransmission(); // on evoie les octets mis en attente et on termine le transmission 

     Wire.beginTransmission(MPU_ADDRESS); // on envoie l'adresse 0x68 au MPU-1 (Slave) pour lancer la transmission  
     Wire.write(0x1C); // ..................... pour communiquer avec le registre ACCEL_CONFIG  
     Wire.write(0x10); //...........    on configure le plage de mesure de l'accélérométre j'usqua  ±8g
     Wire.endTransmission(); //on evoie les octets mis en attente et on termine le transmission   
  
     Wire.beginTransmission(MPU_ADDRESS); //  on envoie l'adresse 0x68 au MPU-1 (Slave) pour lancer la transmission
     Wire.write(0x1A); // ..................... pour communiquer avec le registre CONFIG  
     Wire.write(0x03); //  ................pour activer un filtre passe bas ~43Hz
     Wire.endTransmission(); //on evoie les octets mis en attente et on termine le transmission 
      }

 On suit la meme procedure pour MPU-2. Si vous voulez changer les plage de mesure des Gyros vous avez le choix "250°/S, 500°/S, 1000°/S, 2000°/S" et pour l'accélérométre "+2g, +4g, +8g, +16g".
 
     Pour configurer le Gyro.
 
       0x00 = 250°/S      SSF_GYRO    131
       0x08 = 500°/S      SSF_GYRO    65.5
       0x10 = 1000°/S     SSF_GYRO    32.8
       0x18 = 2000°/S     SSF_GYRO    16.4
       
     Pour configure l'Accel.
       
        0x00 = +2g
        0x08 = +4g
        0x10 = +8g
        0x18 = +16g

   La prochaine partie de code nous permet de récupéré les données brutes des trois axes du gyroscope  de l'accélérométre et la température.

    Wire.beginTransmission(MPU_ADDRESS); // on envoie l'adresse 0x68 au MPU-1 (Slave) pour lancer la transmission  
    Wire.write(0x3B); // on ecrit un octet qu'on place en attente pour communiquer avec le registre ACCEL_XOUT_H
    Wire.endTransmission(); // on envoie l'octet mis en attente et on termine le transmission  
    Wire.requestFrom(MPU_ADDRESS, 14); // On demande les 14 octets  en partan de ACCEL_XOUT_H    

    while (Wire.available() < 14); // tan que les 14 octets ne sont pas recu on attend.

    Rollacc  = Wire.read() << 8 | Wire.read(); // on stoke la valeur d'acceleration du "ROLL" dans la variable "Rollacc"
    Pitchacc  = Wire.read() << 8 | Wire.read(); // on stoke la valeur d'acceleration du "PITCH" dans la variable  "Pitchacc"  
    Yawacc  = Wire.read() << 8 | Wire.read(); //on stoke la valeur d'acceleration du "YAW" dans la variable "Yawacc"
    temperature = Wire.read() << 8 | Wire.read(); // on stoke la temperature dans la variable "temperature"  
    Rollgyro = Wire.read() << 8 | Wire.read(); // on stoke la valeur brute du "ROLL" dans la variable " Rollgyro"  
    Pitchgyro = Wire.read() << 8 | Wire.read(); // on stoke la valeur brute du "PITCH" dans la variable " Pitchgyro" 
    Yawgyro = Wire.read() << 8 | Wire.read(); //  on stoke la valeur brute du "YAW" dans la variable " Yawgyro" 

  La partie du code qui a du surement vous interpeller ses "Wire.read() << 8 | Wire.read()".Que fait cette ligne de code ?
  Elle appelle un octet le decale de 8 bits sur la gauche puis appelle un nouvell octet quel va comparer au premier avec le comparateur binaire "ou". La valeur finale et écrite sur deux octets, je vais vous montrer un exemple ci-dessous.

      ACCEL_XOUT_H = 11000000  // premier octet appellé
      ACCEL_XOUT_L = 00010000  // Deuxiéme octet appellé
         
                 N° 7  6  5  4  3  2  1  0
                    1  1  0  0  0  0  0  0
                    
                           <<8
                   
                N° 15  14 13 12 11 10 9  8  
                    1  1  0  0  0  0  0  0  
                             
                        | Wire.read();        = 1101000000010000
                   
                N° 7  6  5  4  3  2  1  0
                   0  0  0  1  0  0  0  0

Le Gyro meme au repos est trés sensible au vibration "bruit" ce qui a pour effet de faire dérivée notre mesure pour éviter cela  a chaque fois que vous allumerez votre drone on va faire une moyenne du bruit pour chaque axe puis on le soustraira a la valeur brute.

      void Emoyen(){
    int max_samples = 2000;
    for (int i = 0; i < max_samples; i++) { // moyenne n = 2000 on boucle 2000 fois
    lectureMPU(); // on appelle les valeurs brutes 
     
    // on incrémentes les valeurs brutes pour chaque axe 2000 fois
    Eroll += Rollgyro; 
    Epitch += Pitchgyro;
    Eyaw += Yawgyro;
    PORTD |= B11110000; // on mes nos moteur a 0
    delayMicroseconds(1000);
    PORTD &= B00001111;
    
    delay(3);
    } // 0n divise par l'effectif 2000 pour avoir la moyenne des variations au repos
      Eroll /= max_samples; 
    Epitch /= max_samples;
    Eyaw /= max_samples;

    }

 Aprés avoir fait la moyenne des variations. On va voir la partie qui va nous permettre de transformer les valeurs brutes du gyroscope en angle.

      void ANgyro() {
     // on soustrai a chaque boucle la moyenne des variations au valeurs brutes
     Rollgyro -= Eroll;
     Pitchgyro -= Epitch;
     Yawgyro -= Eyaw;

    // on calcul l'angle par integration
    angleRO += (Rollgyro / (FREQ * SSF_GYRO));
    anglePO += (-Pitchgyro / (FREQ * SSF_GYRO)); 
     }

  Pour calculer l'angle on intégre la rotation angulaire toute les 4ms vu que notre programme fonctionnent a 250 Hz. Notre valeur brute divisée par la valeur inscrite sur la datasheet en fonction de la plage de mesure que l'on a configurée nous donne la vitesse de déplacement °/S. Je vais vous donner des exemples si votre plage de mesure est de 500 °/S la valeur donner par la datashett ces 65.5 si l'on fait "500 * 65.5 = 32750" ce qui veut dire que la valeur brute maximale qu'on recevra sera 32750 quand le drone se déplace a 500°/S "32750 /65.5 = 500 °/S" nous savon que notre programme boucle toute les 4 ms si nous recevont 32750 ca veut dire que notre drone se deplace de 500 degrés en une seconde mes vue que nous savons qu'il c'est écoulé 4ms qui représente 1/250 de seconde on fait "500/250 = 2" se qui nous donne de combien de degrés ses déplacer le drone "2°" et a chaque boucle on incrémente l'angle parcouru pour avoir notre position en degrés.
  
  Si vous avez choisi une autre plage de mesure changer la valeur de la variable "SSF_GYRO" plus votre plage de mesure est grande moins le Gyro est précis.
  
    250 °/S   Precision: 1/131 = 0.007°/S
    500 °/S   Precision: 1/65.5 = 0.015°/S
    1000 °/S   Precision: 1/32.8 = 0.03°/S
    2000 °/S   Precision: 1/16.4 = 0.06°/S

La suite du code dans la fonction ANgyro() va nous permettre de transferer l'angle du pitch vers le roll et vis versa en fonction du yaw. Imaginez votre drone penchez vers l'arriére si vous faites tournez le drone autour de l'axe du "YAW" les valeurs de l'axe du Roll et du PITCH ne changerez pas car elle ne suibissent pas d'acceleration.
         
    void ANgyro() {
    anglePO += angleRO * sin(Yawgyro * (PI / (FREQ * SSF_GYRO * 180))); // transfer du Roll sur le PITCH sinus(radians)
  
    angleRO -= anglePO * sin(Yawgyro * (PI / (FREQ * SSF_GYRO * 180))); // // transfer du PITCH sur le ROLL sinus(radians)
    }
    // sin(-90) = -1 , sin(90) = 1,    (  -30°= 30° * sin (90°)

Aprés avoir calculer les angles d'inclinaison avec le gyroscope nous allons calculer les angles avec l'accélérométre.

      void ANacc(){
                                                 
      //  Norme du vecteur acceleration ||X,Y,Z|| = √(X² + Y² + Z²): https://www.youtube.com/watch?v=tTaP48b4_5w
      acc_total_vector = sqrt(pow(Rollacc, 2) + pow(Pitchacc, 2) + pow(Yawacc, 2));
      
      if (abs(Rollacc) < acc_total_vector) {// on s'assure que la valeur reste entre -1 et 1 pour la fonction asin
      RollaccA = asin((float) Pitchacc/ acc_total_vector) * (180 / PI);// on calcule l'angle en radians grace a la fonction asin                 
    }                                                                   puis on la covertie en degrés "180/3.14 = 1rad/57.32°

    if (abs(Pitchacc) < acc_total_vector) { // on s'assure que la valeur reste entre -1 et 1 pour la fonction asin
    PitchaccA = asin((float)Rollacc/ acc_total_vector) * (180 / PI);// on calcule l'angle en radians grace a la fonction asin                 
    }                                                                 puis on la covertie en degrés "180/3.14 = 1rad/57.32°
    
    }
    
    // arcsin prend le sinus de l'angle (Pitchacc(coté opposé)/ acc_total_vector(hypothénuse)) est renvoie l'angle.
       Regardez l'image suivante.

   
   
   Maintenant que nous avons les angles du Gyro et de l'accélérométre nous allons fusionner les deux mesures. Le Gyro a pour avantage de ne pas étre sensible au vibration mes la mesure dérive au contraire l'accélérométre ne dérive pas mes est trés sensible au vibration donc les deux mesures se compense et en les fusionnant on aura de meilleur résultat l'angle ne dérivera presque pas dans le temps.
   
   Le Gyro dérive car nous prenons une valeur toute les ~4ms et nous considérons que la vitesse angulaire est la méme pendant les 4ms alors quand réalité ses faut. L'accélérométre ne dérive pas car il mesure l'angle en utilisant l'apesanteur terrestre 9.81 m-s. D'ailleurs nous verrons juste aprés dans la partie ou l'on fusionne les deux mesures et que plus votre programme a une frequence élevé moins nous utilisons la mesure de l'accelérométre.

    void calculangle () {
    
    if (initialized) {
    // (gyro * (1-temps parcouru pour une boucle) + Accel * (temps parcourue pour une boucle)
    angleRO = angleRO * 0.996 + RollaccA * 0.004; 
    anglePO = anglePO * 0.996 +  PitchaccA* 0.004;
    } else {
    //La premiere mesure est faite seulement par l'accelerometrre 
    angleRO = RollaccA;
     anglePO= PitchaccA;
    initialized = true;
    }
    }
    
    // Si vous voyez que votre angle dérive n'hésitez pas a modifier les coefficient utiliser pour la fusion des données.

 Dans la prochaine partie on rajoute un second filtre pour ameliorez la precision puis on calcule est filtre la vitesse de déplacement "°/S" autour des axes.

    void calculangle () {
    
    angleR  = angleR * 0.9 + angleRO * 0.1; // on utilise de nouveau un filtre complementaire
    angleP = angleP * 0.9 + angleRO1 * 0.1;
    // on calcule les "°/S" pour chaque axe est on les filtres "filtre passe-bas 10hz"
    ASR = (ASR * 0.7) + ((Rollgyro / 65.5) * 0.3);    
    ASP = (ASP * 0.7) + ((Rollgyro1 / 65.5) * 0.3); 
    ASY = (ASY * 0.7) + ((Yawgyro/ 65.5) * 0.3);   
    
    }

 Mon programme utilisent deux gyroscopes a 90° car l'axe du pitch ne fonctionne pas, le drone etait completement instable. J'ai essayer de trouver le probléme en regardant si l'angle du pitch indiquer par le Gyro correspondait a son angle réelle est je n'ai pas vue de probléme, je me suis  dit que sa devais etre le régulateur PID j'ai alors tourner le gyroscope de 90° sur le drone de sorte que l'axe du PITCH du GYRO soit sur l'axe du ROLL du drone et le PITCH du drone sur l'axe du ROll du GYRO et mon drone et devenu instable sur l'axe du ROLL ce qui montre que le probléme ne vient pas du PID. J'ai aussi fait un "Self-test" qui nous permet de tester si le Gyro et l'Accel non pas de probléme mechanique ou électrique mais les résultat etait proche des valeurs d'usine.  J'essayerais mon drone avec un seul Gyro neuf l'orsque je l'aurais recu. Pour l'instant avec les deux gyroscopes le drone fonctionnent bien et reste stable . Les programmes "" et "" n'utilisent qu'un Gyro essayait les sur un bac de test pour voir si sa fonctionnent.

 - Amelioration
 
 Le controleur de vol que nous avons fait est trés loin d'étre optimal pour plusieurs raisons. 

 -Le drone ne restera pas sur place, pour qu'il le reste il faudrait ajouté un magnétométre et un GPS qui nous permettrait d'avoir la position(longitude, latitude), l'altitude et la direction du drone. L'orsque vous n'actionnées pas les commandes du "ROLL" et du "PITCH" le programme stoke la position et l'altitude du drone grace au gps et un régulateur P.D va se charger de maintenire la position et l'altitude. Vous pouvez aussi implementez un programme qui en cas de perte de signal reviens vers vous dans ce cas il faut enregistrer la position quand vous faites d'écollé votre drone et l'altitude maximale atteinte pendant le vol. il faut definir une variable qui stok le gain d'altitude, quand on pert le signal le drone remontera a l'altitude maximale atteinte pendant le vol plus le gain d'altitude. Si vous voulez plus d'information je vous invite a aller voir l'exellente série de video de Joop Brokking: https://www.youtube.com/channel/UCpJ5uKSLxP84TXQtwiRNm1g

 - La fréquence d'échantillonage de notre programme est de 250Hz pour le Gyro&Accel et le P.I.D ce qui est trés faible comparé au carte de vol disponible dans le commerce qui peuvent échantilloner facilement en 4Khz j'usqua 32Khz pour les meilleurs carte. Notre drone peut voler car il n'est pas particuliérement rapide et nerveu, les drones les plus rapide dépassent les 300K/MH sur ce type de drone notre controleur de vol ne pourrait pas fonctionné car notre drone parcour une distance trop grande alors que le Gyro na fait qu'une mesure. Haugmentez la frequence nécéssitent un réglage des filtres car le Gyro a un biais moin important vu que l'incrémentation de l'angle est faite plus souvent mais en contrepartie la sensibibilité au bruit augmente. Est la vous allez vous demander pourquoi on augmente pas la frequence en modifiant tous simplement la ligne de code suivante "while (micros()-prevmicros < 4000);" et la variable "FREQ" ?  Les MiCro de l'arduino uno ou mega ont une frequence de 16Mhz et ne nous permette pas de faire tourner notre programme a plus de 250Hz l'arduino n'est pas fait pour de t'elle application il est généralement utiliser pour voir si un protype fonctionnent.
 
 Les controleurs de vol disponible dans le commerce on en général des MiCro stm32 qui se decline en plusieurs versions "F4,F7,H7...." qui peuvent fonctionner a des fréquences beaucoup plus élevée 216Mhz pour le "F7" et ~450MHZ pour le "H7" les différentes version ont aussi plus ou moins de memoire ce qui permet de rajouter des fonctionnalités. Il existe une carte de dévellopement qui a un MiCro stm32 F7 "NUCLEO-F722ZE" avec cette carte vous pourrait lire les données du Gyro&Accel  beaucoup plus vite et faire tourner aussi plus vite les régulateur P.I.D.

 Maintenant que vous avez un MiCro plus performant on va s'interesser au différente centrale inertielle disponible sur le marcher.

 -Le MPU-6000 a une bonne tolérance au vibration et peut  communiquer les données du Gyro a 8Khz et de l'Accel a 1Khz en utilisant le protocole de communication SPI
 
 -Le MPU-6050 que nous utilisons peut étre utiliser seulement avec le protocole de communnication I2C 400Khz qui limite la vitess delecture du Gyro a environ 2Khz et de l'Accel a 1Khz il et rarement utilisé sur les carte de vol.

 -Le MPU-6500 peut fonctionner j'usqua 32Khz avec le protocole de communication SPI si vous avez un MiCro F4 ou F7.

 -Le ICM20602 a été spécialement concu pour les drones il censé étre moins sensible au bruit et fonctionnent aussi en 32Khz mais d'aprés des tests il serait beaucoup plus sensible au bruit.

 https://www.wearefpv.fr/filtres-betaflight-tuning-en-3-5-et-plus-20190202/
 
 https://blog.dronetrest.com/inertial-sensor-comparison-mpu6000-vs-mpu6050-vs-mpu6500-vs-icm20602/

https://www.youtube.com/watch?v=bCEiOnuODac

Frame impression 3D .

Controleur de vol P.I.D: arduino Uno ou arduino Mega. 
https://www.youtube.com/watch?v=yRw2mC_6A00

 

  



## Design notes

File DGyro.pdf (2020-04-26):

M2206 - Développement des Compétences Projet

## Inclinomètre : Dossier Technique

## Table des matières

DUT GEII - S2 | M2206 | 1/14

## 1 Présentation

### 1. Introduction

Le projet vise à réaliser un inclinomètre semblable à celui utilisé dans la plupart des smartphones, et qui permettra de connaître le degré d'inclinaison d'un objet solidaire de la carte électronique à développer.

On peut définir l'inclinaison d'un objet selon 3 axes
- le roulis (Roll) , le tangage (Pitch) et le lacet (Yaw) :

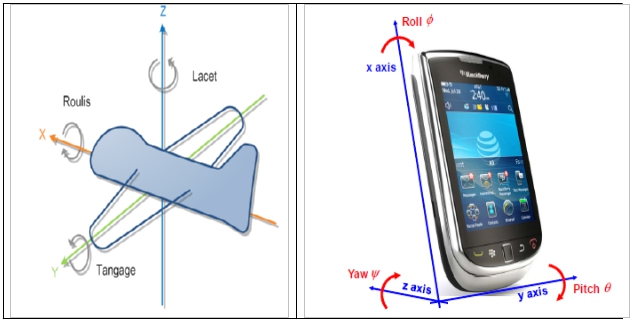
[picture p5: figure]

### 2. Principe de l'accéléromètre

Un accéléromètre sert à mesurer une accélération, mais il est possible de s'en servir pour mesurer l'inclinaison d'un objet immobile. En effet, l’accéléromètre ne fait pas la différence entre l'accélération et la gravité . Lorsqu'il est immobile, l'accéléromètre mesure, en fait, le champ gravitationnel.

Pour être plus précis, l'accéléromètre mesure la composante de la force de gravité selon 3 axes:
- l'axe des x (orienté selon le sens de la longueur)
- l'axe des y (orienté selon le sens de la largeur) et
- l'axe des z (orienté perpendiculairement à la surface).

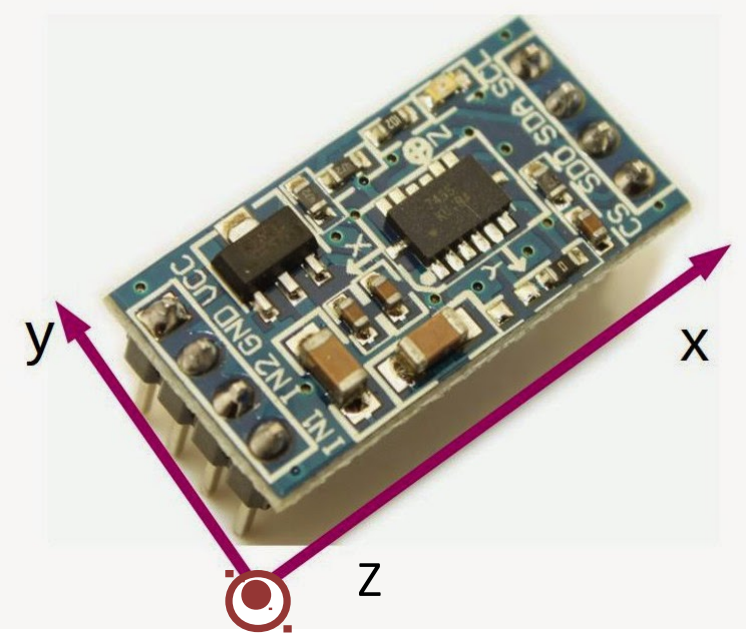
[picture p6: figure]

Rappel : Composantes Gx et Gz de la gravité G ( exemple avec 2 axes )

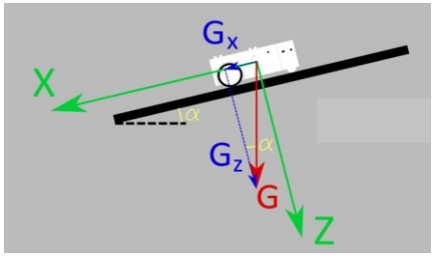
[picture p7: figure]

Un des principaux objectifs de votre projet est la détermination des angles d'inclinaison (angle α de la figure ci-dessus pour le tangage).

Un accéléromètre fournit donc 3 tensions (Vx, Vy et Vz) proportionnelles aux composantes X, Y et Z de la gravitation g.
Une carte électronique lui sera associée pour permettre une mise à l’échelle de ces tensions entre 0 et 5 V.

### 3. ADXL335

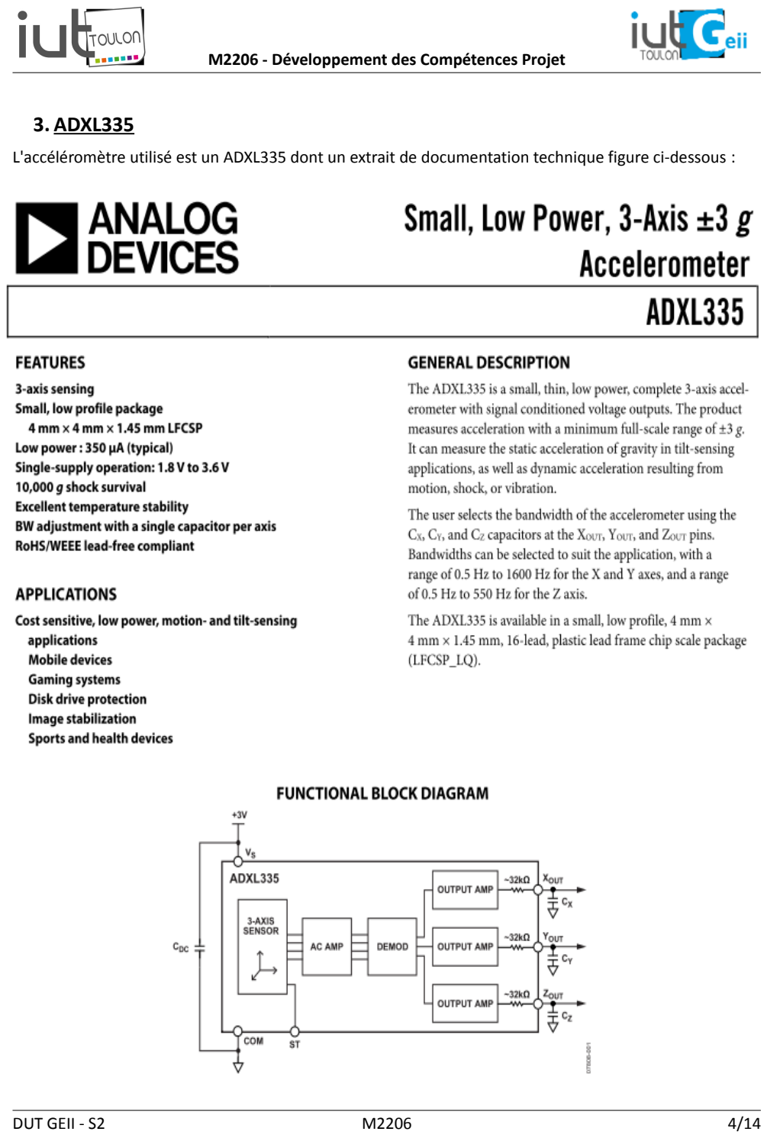
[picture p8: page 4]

L'accéléromètre utilisé est un ADXL335 dont un extrait de documentation technique figure ci-dessous :

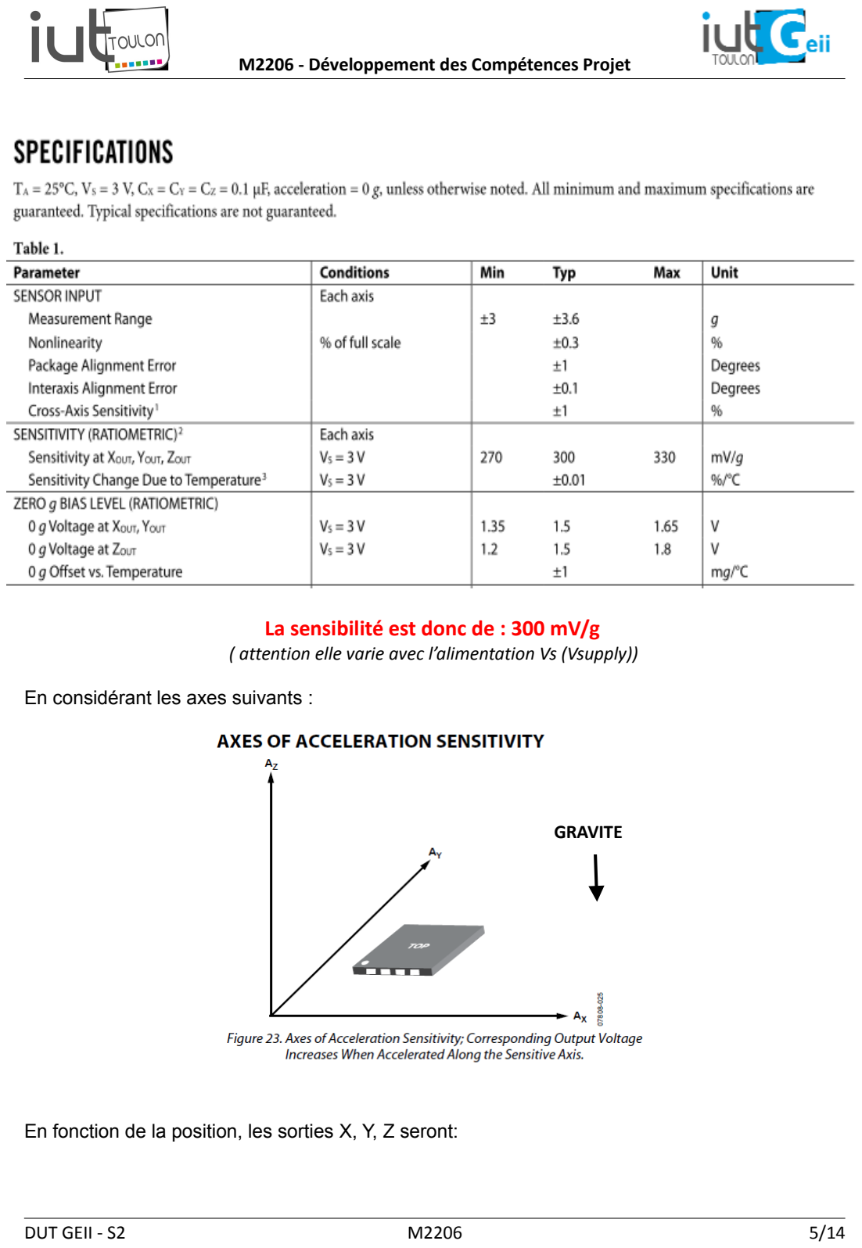
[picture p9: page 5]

La sensibilité est donc de : 300 mV/g
( attention elle varie avec l’alimentation Vs (Vsupply))

En considérant les axes suivants :

En fonction de la position, les sorties X, Y, Z seront:

GRAVITE

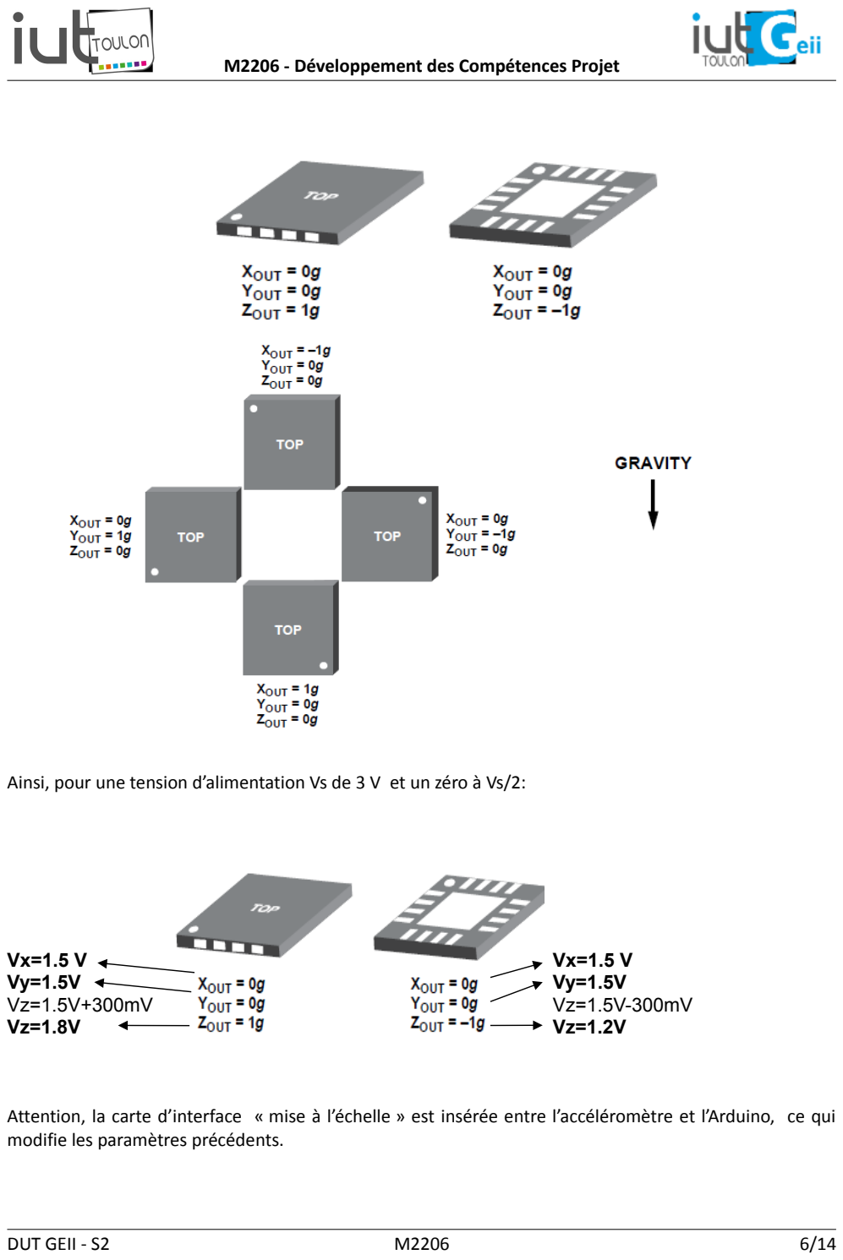
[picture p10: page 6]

Ainsi, pour une tension d’alimentation Vs de 3 V et un zéro à Vs/2:

Vx=1.5 V
Vy=1.5V
Vz=1.5V+300mV
Vz=1.8V

Vx=1.5 V
Vy=1.5V
Vz=1.5V-300mV
Vz=1.2V

Attention, la carte d’interface « mise à l’échelle » est insérée entre l’accéléromètre et l’Arduino, ce qui modifie les paramètres précédents.

### 4. Calcul des angles

Reprenons l’exemple précédent :

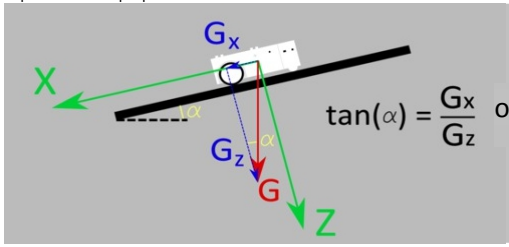
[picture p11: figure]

Fig. 1

Il faut extraire la valeur de Gx, Gy et Gz des tensions Vx, Vy et Vz de la manière suivante :

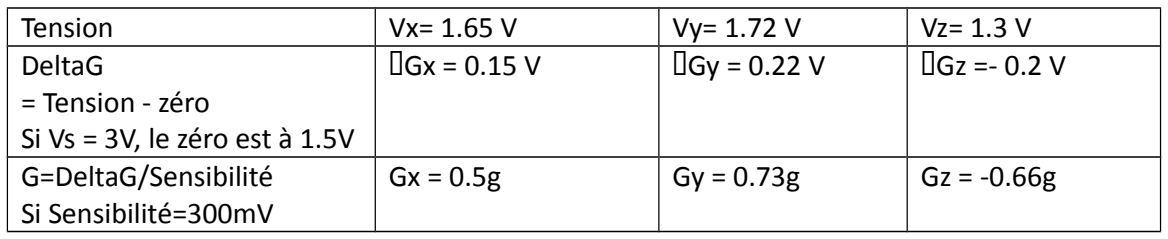
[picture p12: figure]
Tension; DeltaG = Tension - zéro Si Vs = 3V, le zéro est à 1.5V; ΔGx = 0.15 V; ΔGy = 0.22 V; ΔGz =- 0.2 V; G=DeltaG/Sensibilité Si Sensibilité=300mV

On en déduit les angles de la manière suivante (voir figure 1) :

soit (tan(α)=

GX
GZ

) (α=arctan(

GX
GZ

)) → C’est l’angle de roulis (roll)

De la même façon :

soit (tan(ϕ )=

GY
GZ

) (ϕ =arctan (

GY
GZ

)) → C’est l’angle de tangage (pitch)

La norme du vecteur de gravitation g sur 3 axes, en fonction des ses composantes sur x, y et z s'écrit : √(GX
2
+GY

2
+GZ

2
)

# ou sin (α)=

On en déduit donc l'expression des 3 angles d'inclinaison qui nous intéressent :

- Roulis : (α=arcsin(

GX
(√(GX
2
+GY

2
+GZ

2
))

))

- Tangage : (ϕ =arcsin (

GY
(√(GX
2
+GY

2
+GZ

2
))

))

- Verticalité : (α=arccos(

GZ
(√(GX
2
+GY

2
+GZ

2
))

))

### 5. Matériel

Les différents sous-ensembles constitutifs du projet final seront :
- La carte de développement arduino UNO
- Un circuit ADL335
- La carte électronique de mise à l'échelle des signaux de l'accéléromètre
- Un afficheur LCD pour arduino LCD1602

## 2. Partie Électronique : Carte de Mise à l'échelle

### 1. Objectif

Le but de cette partie est de permettre la meilleure acquisition possible des tensions délivrées par l'accéléromètre par le convertisseur A/N du microcontroleur.
Pour cela, il faut que les plages des tensions en entrée du convertisseur soient le plus proche possible de la gamme [ 0V ; Vref+] → [0V ; 5V]
La fonction de transfert idéale de cette carte électronique pourrait donc être résumée par la droite suivante :

### 2. Contraintes

L'alimentation de cette carte se fera en monotension (0-5V), afin d'être compatible avec une application "embarqué" (alimentée par une batterie).
Il faudra donc choisir des A.O compatibles avec ce type d'alimentation, et offrant notamment une plage de tensions de sorties "rail to rail", c'est à dire dont la saturation n'apparaît que lorsque la tension de sortie est atteinte.
En pratique, les limites du circuit choisi feront que l'on ne pourra que s'approcher de la fonction de

Vx, Vy, Vz

V
CAN1

, VCAN2

, VCAN3
5V
0V | 1,35 1,5 | 1,65

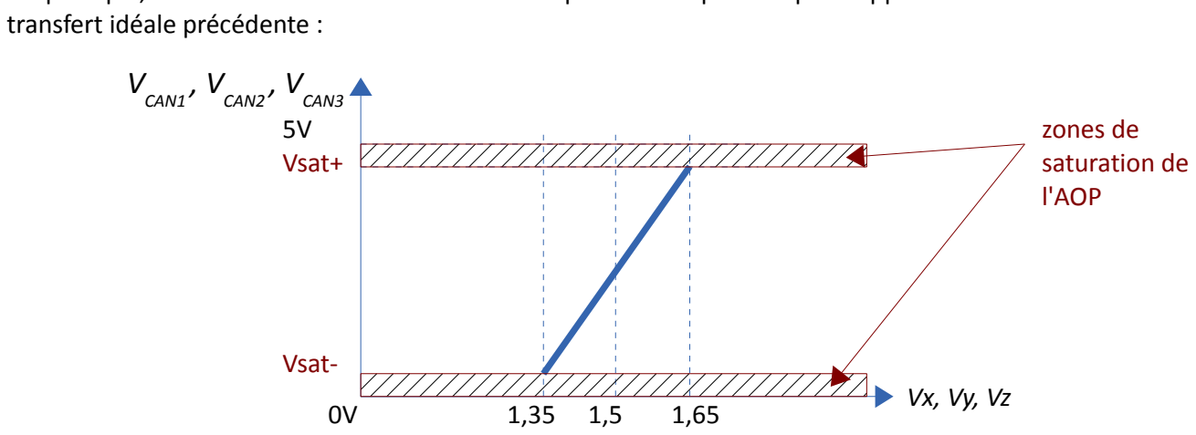
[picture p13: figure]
transfert idéale précédente :; 5V Vsat+; Vsat-; V CAN1; , VCAN2; , VCAN3; zones de saturation de l'AOP

### 3. MC33 0 02

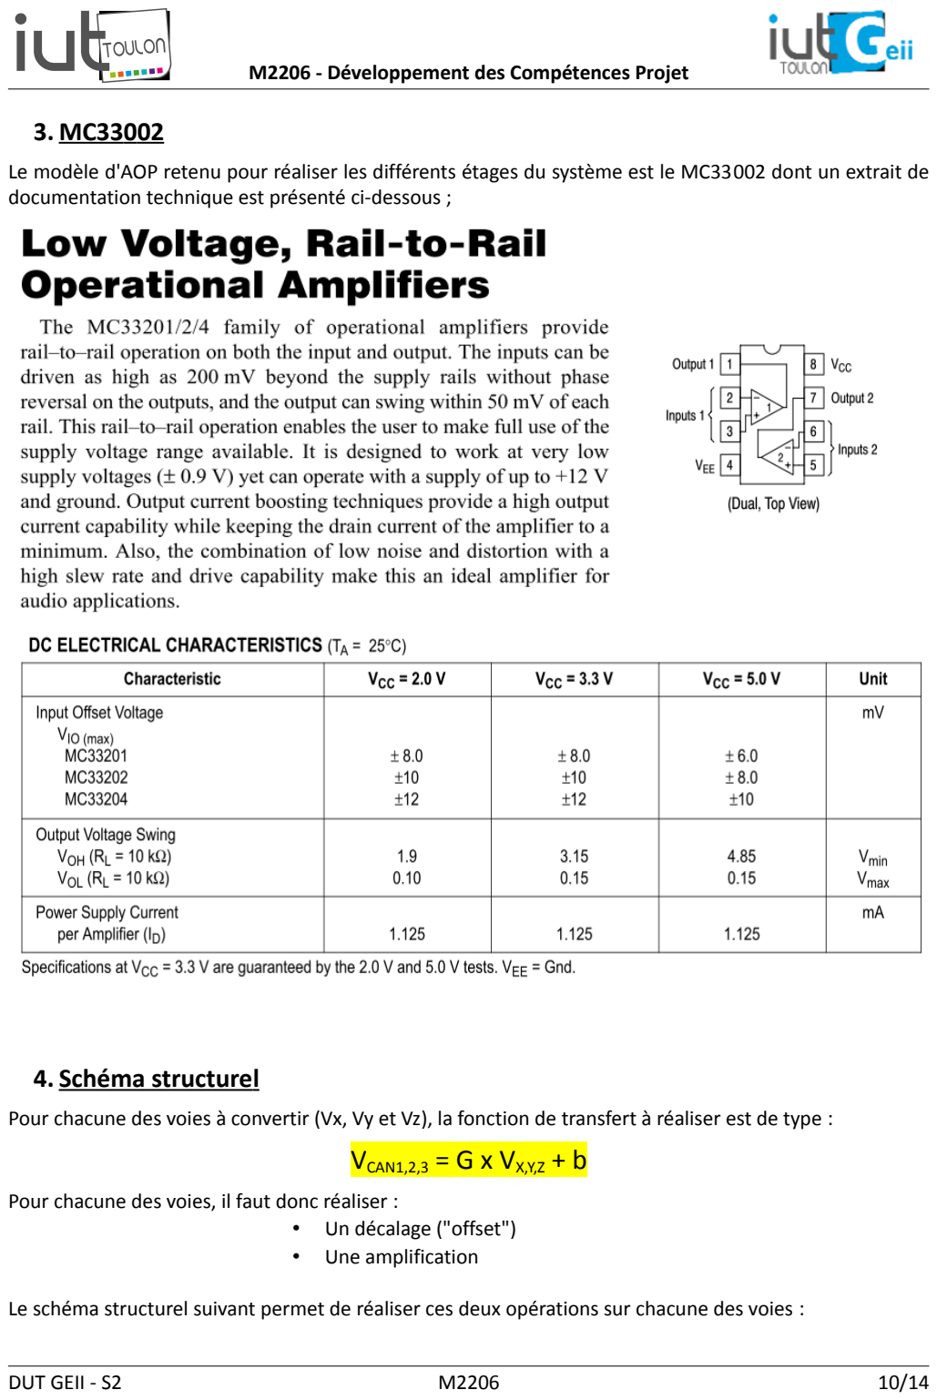
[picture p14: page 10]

Le modèle d'AOP retenu pour réaliser les différents étages du système est le MC33002 dont un extrait de documentation technique est présenté ci-dessous ;

### 4. Schéma structure l

Pour chacune des voies à convertir (Vx, Vy et Vz), la fonction de transfert à réaliser est de type :

VCAN1,2,3 | = G x VX,Y,Z | + b

Pour chacune des voies, il faut donc réaliser :
- Un décalage ("offset")
- Une amplification

Le schéma structurel suivant permet de réaliser ces deux opérations sur chacune des voies :

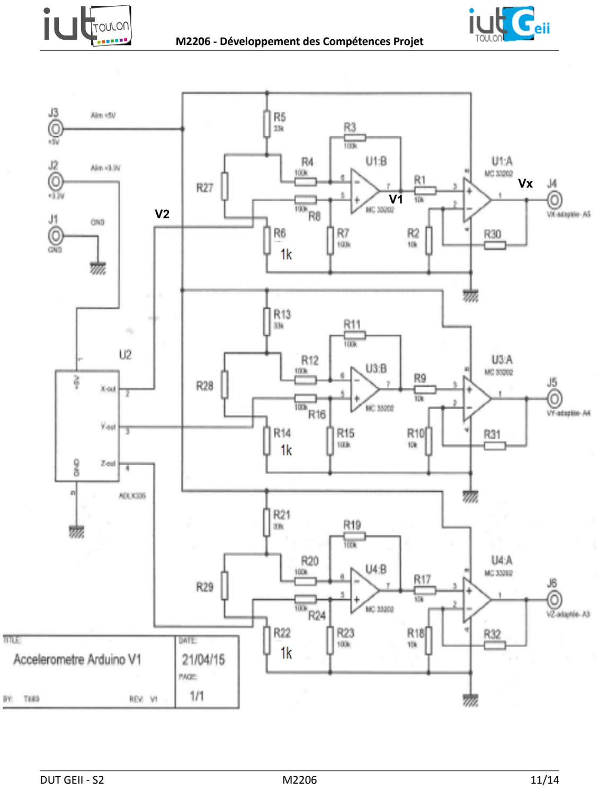
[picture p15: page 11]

V2

V1

Vx

### 5. Nomenclature des Composants

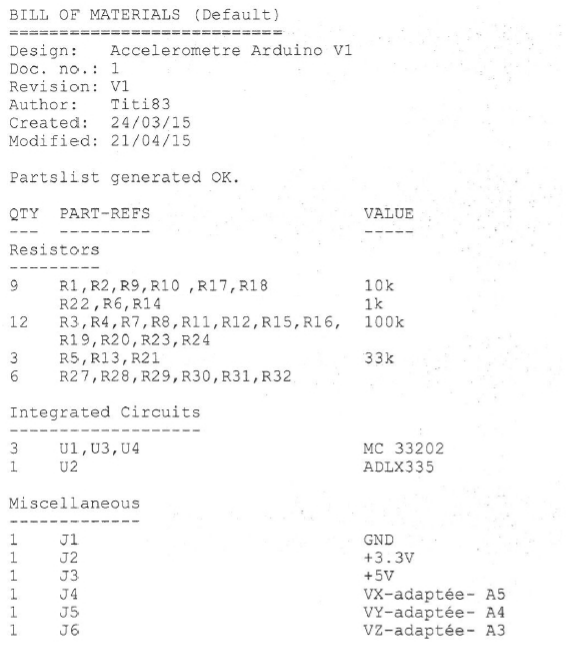
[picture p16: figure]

### 6. Travail à réaliser

- Tâche 0 : Fabrication de la carte
→ Réaliser la carte en technologie CMS (perçage des trous, placement des composants CMS, passage au four...)
- Tâche 1 : Calculs des fonctions de transfert → Déterminer la F.T globale de chacune des voies en fonction des éléments du schéma
- Tâche 2 : dimensionnement des composants → Déterminer dans la série E12 la résistance R27(R28, R29) qui permet d’ obtenir V1≈0 à V2min
→ Déterminer dans la série E12 la résistance R30 (R31, R32) qui permet d’obtenir. Vx=5V à V2max (XOUTmax)

## 3. Partie Codage : Arduino

### 1. Objectifs

L'objectif de cette partie est la réalisation d'un programme qui permettra le calcul des angles de roulis, tangage et lacet à partir des tensions issues de l'accéléromètre (et mises à l'échelle) ; et de transmettre ces valeurs sur une liaison série afin de permettre leur exploitation par une interface graphique. Un affichage "local" sera en outre réalisé sur un écran LCD.

### 2. Travail à réaliser

La décomposition du travail à effectuer répond au découpage suivant :
- Tâche 0 : Création d'un programme "squelette"

→Création d'un programme incluant les bibliothèques et définitions nécessaires au projet, ainsi qu'une boucle infinie rythmée à 5Hz (ne pas utiliser delay mais millis)

- Tâche 1 : Acquisition des voies analogiques

→ Définir les voies à convertir, coder l'acquisition de façon à ce que les données soient rafraîchies à la fréquence de 5Hz et affichées dans le moniteur série .

- Tâche 2 : Utilisation d'un émulateur de terminal (type hyperterminal)

→ Lire ces valeurs non plus dans le moniteur série dans dans un émulateur de terminal (type hyperterminal)

- Tâche 3: Calcul des angles de tangage, de roulis et de lacet

→ implanter les calculs décrits dans la présentation du document.

- Tâche 4 : Affichage sur l'écran LCD

→ Étude du module LC1602 board et recherche des fonction logicielles associées, codage de l'affichage (pensez à ne réécrire que le nécessaire à chaque boucle)

## 4.Partie IHM : Labview

### 1. Objectifs

Réaliser une interface graphique pour PC permettant l'affichage des différents angles sous forme de vu-mètres et de cadrans numériques, à partir des données récoltées sur la liaison série.

### 2. Travail à réaliser

- Tâche 0 : Prise en main de Labview

→ exécution d'un tutoriel.

- Tâche 1 : Paramétrage de la L.S

→ Validation avec hyperterminal : affichage de valeurs numériques saisies sous H.T

- Tâche 2 : Affichage des données Gx, Gy et Gz brutes

→ Affichage des valeurs sous forme de cadran numérique

- Tâche 3: Calcul des angles de tangage, de roulis et de lacet et affichage en "vu-mètre"

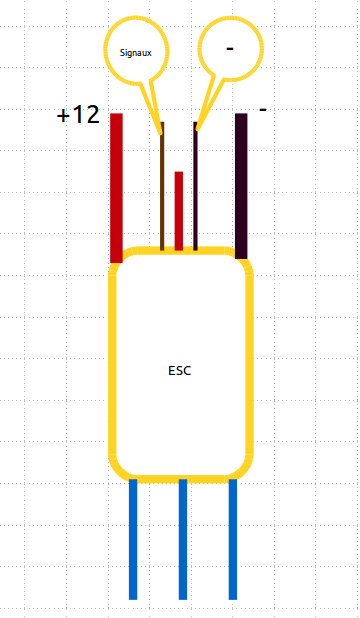
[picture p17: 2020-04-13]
ESC.png

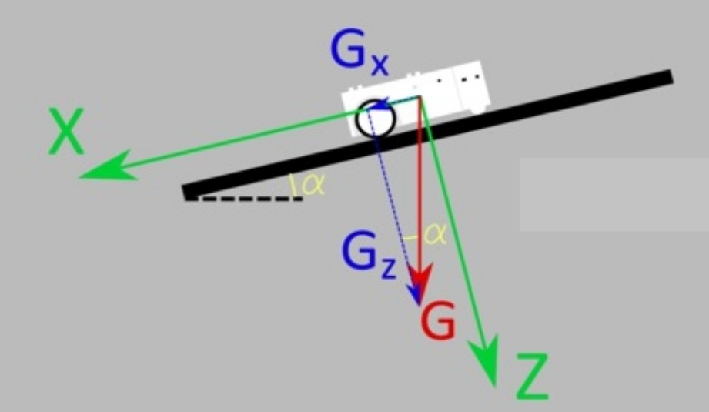
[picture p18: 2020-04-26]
ARCSIN.png

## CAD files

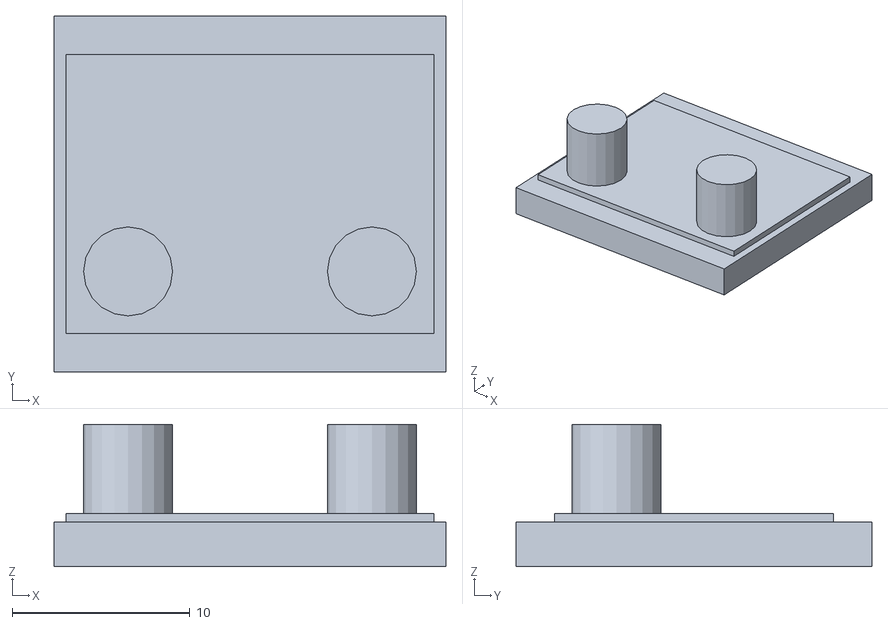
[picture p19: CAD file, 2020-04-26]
N.SupMPU6050.stl
22.0 x 20.0 x 8.00

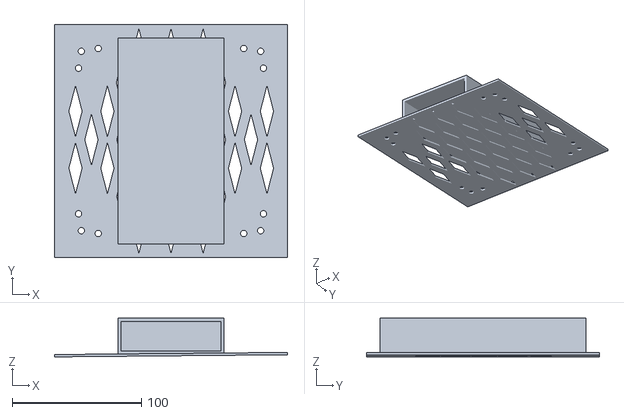
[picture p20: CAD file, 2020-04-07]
N.bas drone.stl
180.0 x 180.0 x 30.0

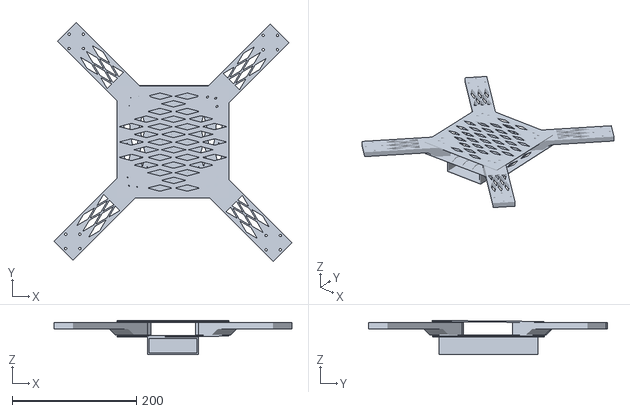
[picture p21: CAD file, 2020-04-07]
Drone.montage.stl
383.2 x 384.6 x 55.0

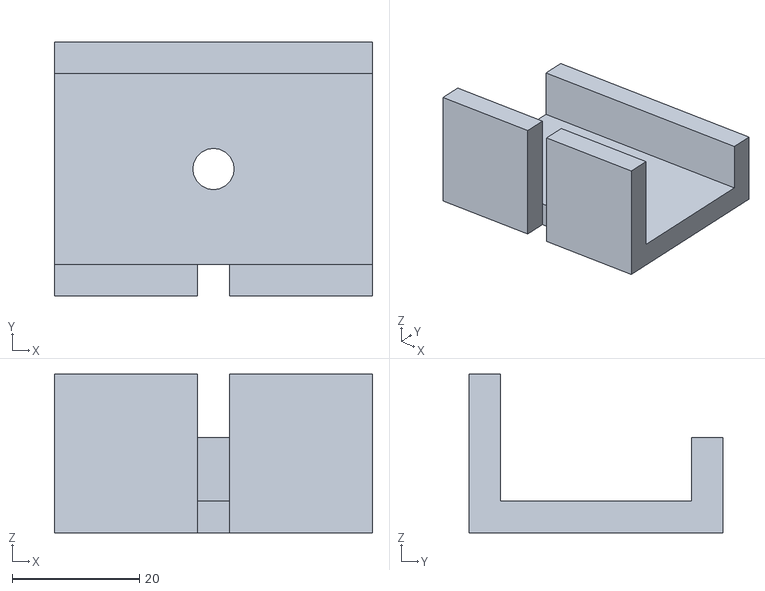
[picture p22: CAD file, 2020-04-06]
N.calibra.stl
50.0 x 40.0 x 25.0

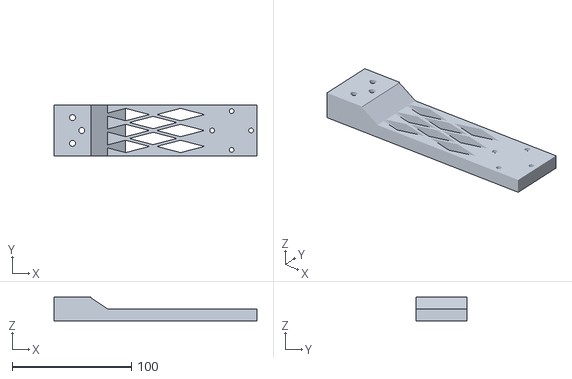
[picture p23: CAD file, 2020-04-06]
N.bras.stl
170.0 x 43.0 x 20.0

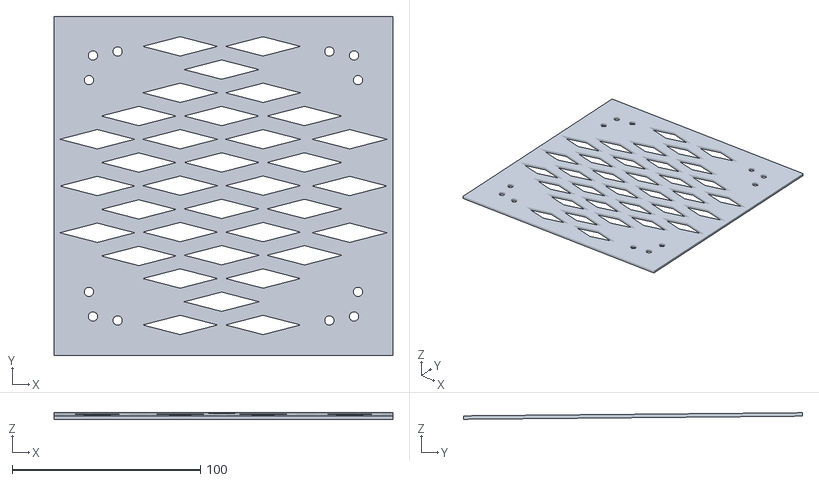
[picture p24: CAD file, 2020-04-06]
N.ruche.stl
180.0 x 180.0 x 3.50

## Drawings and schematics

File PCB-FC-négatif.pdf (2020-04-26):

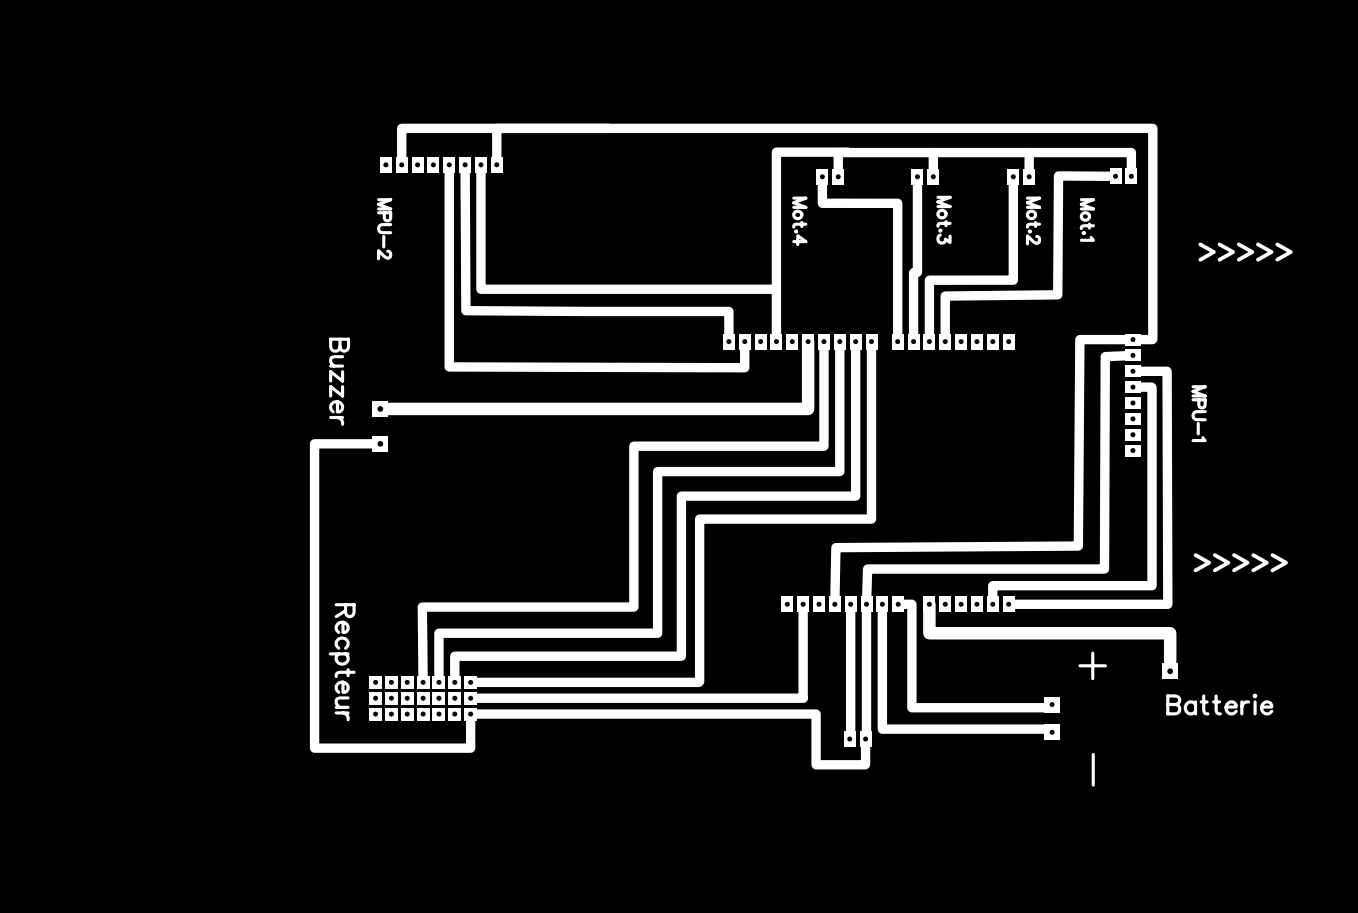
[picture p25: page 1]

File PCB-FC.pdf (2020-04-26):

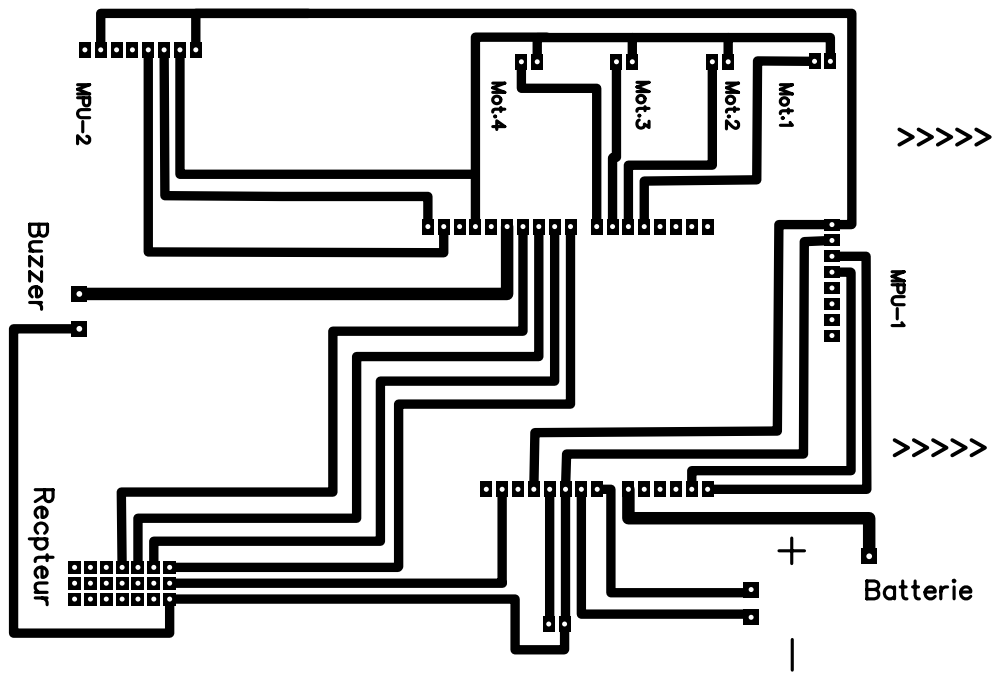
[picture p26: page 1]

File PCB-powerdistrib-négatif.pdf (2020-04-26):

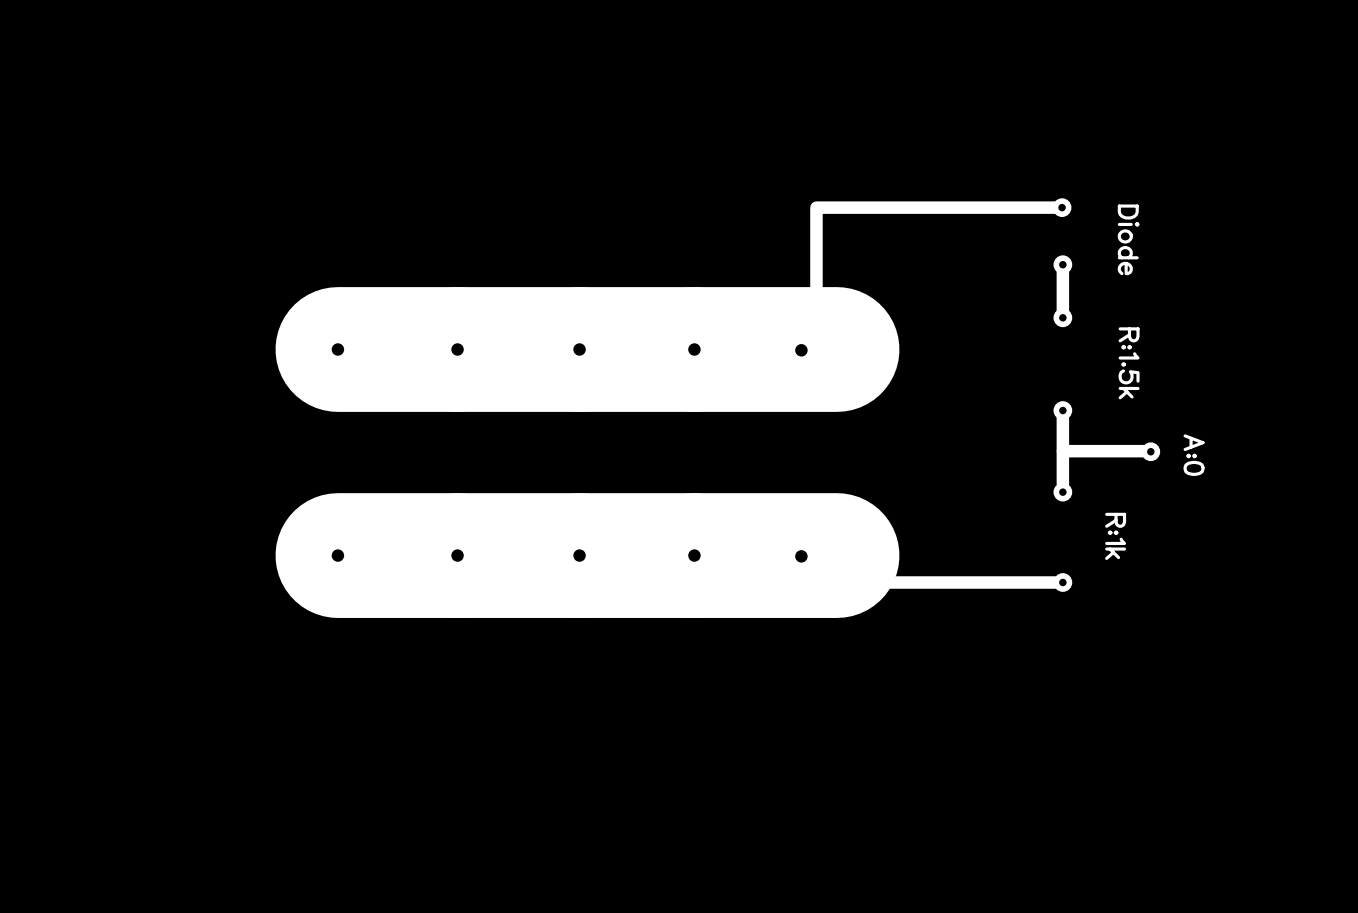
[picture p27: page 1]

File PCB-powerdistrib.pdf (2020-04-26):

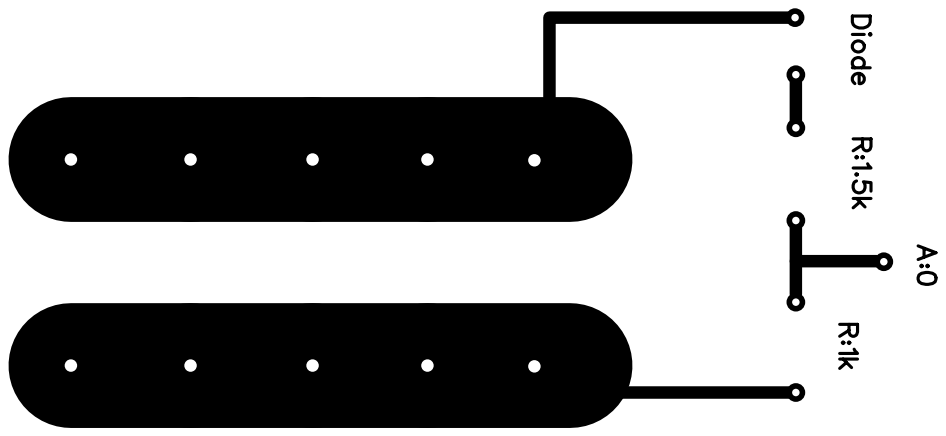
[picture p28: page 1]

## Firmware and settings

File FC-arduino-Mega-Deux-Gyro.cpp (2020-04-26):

#include <Wire.h>
#include "I2Cdev.h"
#include "MPU6050.h"
MPU6050 mpu(0x68);
MPU6050 mpu1(0x69);

#define MPU_ADDRESS 0x68  // I2C address of the MPU-6050
#define MPU_ADDRESS1 0x69
#define FREQ        250   // Sampling frequency
#define SSF_GYRO    65.5  // Sensitivity Scale Factor of the gyro from datasheet

boolean initialized;
long Eroll, Epitch, Eyaw,  acc_total_vector, premicros,Eroll1, Epitch1, Eyaw1,  acc_total_vector1;
int Rollgyro, Pitchgyro, Yawgyro, Rollacc, Pitchacc, Yawacc, temperature,Rollgyro1, Pitchgyro1, Yawgyro1, Rollacc1, Pitchacc1, Yawacc1, temperature1;
float angleRO, anglePO,RollaccA , PitchaccA,angleRO1, anglePO1,RollaccA1 , PitchaccA1;

volatile unsigned long timer[6];
volatile unsigned long current_time;
volatile byte previous_state[6];
volatile unsigned int pulse_duration[6] = {1500, 1500, 1500, 1000,1000,1000};



float KYP = 0; // Coefficient YAW 4  0.02
float KYI = 0;
float KYD = 0;

float KRP = 1.3;
float KRI = 0.04;
float KRD = 18;//18;

float KPP = 1.3; //1.3;// Coefficient Pitch
float KPI =0.04; //0.04;
float KPD =18;//18;

float anglemaxP, anglemaxR, ConsG,  ConsP,  ConsR,  ConsY, EpropP,  EpropR,  EpropY,  EintP,  EintR,  EintY, EdevP, EdevR, EdevY, lastEP, lastER, lastEY, EPIDP, EPIDR, EPIDY,batterieV,angleP, angleR,ASP, ASR, ASY;
int mot1, mot2, mot3, mot4 ;
unsigned long prevmicros, prelmicros;
int decollage = 0;
int chanel1; //gaz
int chanel2; //pitch
int chanel3; //roll
int chanel4;  //Yaw
int gros;



void setup(){
Serial.begin(57600);
 PCICR  |= (1 << PCIE0);
 PCMSK0 |= (1 << PCINT0);
 PCMSK0 |= (1 << PCINT1);
 PCMSK0 |= (1 << PCINT4);
 PCMSK0 |= (1 << PCINT3);
 PCMSK0 |= (1 << PCINT5);
 PCMSK0 |= (1 << PCINT7);
batterieV= (analogRead(0) + 65) * 1.2317;
DDRA  |= B11110000;
Wire.begin();
TWBR = 24;
mpu.initialize();
mpu.setXAccelOffset(-3771);
mpu.setYAccelOffset(-1100);
mpu.setZAccelOffset(1106);
mpu.setXGyroOffset(-10);
mpu.setYGyroOffset(70);
mpu.setZGyroOffset(-8);

 mpu1.initialize();
mpu1.setXAccelOffset(497);
mpu1.setYAccelOffset(1703);
mpu1.setZAccelOffset(1148);
mpu1.setXGyroOffset(-629);
mpu1.setYGyroOffset(206);
mpu1.setZGyroOffset(-8);

communication();
Emoyen();


}

void loop(){
 activation();
  lectureMPU ();
 ANgyro();
 ANacc();
 calculangle ();
 consigne();
 PID();
 Signeauxcorrec();
 transmission();

}


void consigne(){

ConsG = 0;
ConsP = 0;
ConsR = 0;
ConsY = 0;

chanel1 =  pulse_duration[3]; //interrupt 11  Recepteur:CH3  "GAZ"
chanel2 =  pulse_duration[1]; //interrupt 9  Recepteur:CH2   "PITCH"
chanel3 =  pulse_duration[2]; //interrupt 10  Recepteur:CH4 "ROLL"
chanel4 =  pulse_duration[0]; //interrupt 8  Recepteur:CH1  "YAW"

if (chanel1 < 1000) chanel1 = 1000;
if (chanel1 > 1800) chanel1 = 1800;
if (chanel2 < 1000) chanel2 = 1000;
if (chanel2 > 2000) chanel2 = 2000;
if (chanel3 < 1000) chanel3 = 1000;
if (chanel3 > 2000) chanel3 = 2000;
if (chanel4 < 1000) chanel4 = 1000;
if (chanel4 > 2000) chanel4 = 2000;
//gaz
  if (chanel1 >1008){
  ConsG = chanel1;
   }


//Pitch
  if (chanel2 >1508){
   ConsP = (chanel2-1508);
   }else if (chanel2 < 1492){
   ConsP = (chanel2-1492);
   }

    //Roll
  if (chanel3 >1508){
   ConsR = (chanel3-1508);
   }else if (chanel3 < 1492){
   ConsR = (chanel3-1492);
   }

     //Yaw
  if (chanel4 >1508){
   ConsY = (chanel4-1508);
   }else if (chanel4 < 1492){
   ConsY = (chanel4-1492);
   }

    anglemaxP = 15 * angleP;
    anglemaxR = 15 * angleR;

    ConsP -= anglemaxP ;
    ConsP /= 3;
    ConsR -=  anglemaxR;
    ConsR /= 3;
    ConsY /= 3;


}



void PID(){
//erreur proportionnelle
EpropP = ASP - ConsP;
EpropR = ASR - ConsR;
EpropY = ASY - ConsY;


//erreur intégré
EintP +=  EpropP;
EintR +=  EpropR;
EintY +=  EpropY;

if ( EintP > 400 ) EintP = 400;
if ( EintP < -400 )EintP = -400;
if ( EintR > 400 ) EintR = 400;
if ( EintR < -400 )EintR = -400;
if ( EintY > 400 ) EintY = 400;
if ( EintY < -400 )EintY = -400;

//erreur derivée
EdevP =  EpropP-lastEP;
EdevR =  EpropR-lastER;
EdevY =  EpropY-lastEY;


lastEP =  EpropP;
lastER =  EpropR;
lastEY =  EpropY;



 
EPIDR = KRP * EpropR + KRI * EintR + KRD * EdevR;
EPIDP = KPP * EpropP + KPI * EintP + KPD * EdevP;
EPIDY = KYP * EpropY + KYI * EintY + KYD * EdevY;



if ( EPIDP > 400 ) EPIDP = 400;
if ( EPIDP < -400 )EPIDP = -400;
if (EPIDR > 400 ) EPIDR = 400;
if (EPIDR < -400 )EPIDR = -400;
if ( EPIDY > 400 ) EPIDY = 400;
if ( EPIDY < -400 )EPIDY = -400;

}


void resetvariable(){
lastEP = 0;
lastER = 0;
lastEY = 0;
 EintP = 0;
 EintR = 0;
 EintY = 0;
 EpropP = 0;
 EpropR = 0;
 EpropY = 0;
}

void activation(){
if(decollage == 0 && chanel1 <= 1008 && chanel4 > 1980 && chanel3 > 1980){
  decollage = 1;
  resetvariable();
}

 if(decollage == 1 && chanel1 <= 1008 && chanel2 > 1980 && chanel4 < 1008){
  decollage = 0;
}



}



void Signeauxcorrec(){
if ( decollage == 1){

mot1 = ConsG-EPIDR-EPIDP-EPIDY;
mot2 = ConsG+EPIDR-EPIDP+EPIDY;
mot3 = ConsG-EPIDR+EPIDP+EPIDY;
mot4 = ConsG+EPIDR+EPIDP-EPIDY;


batterieV = batterieV * 0.92 + (analogRead(0) + 65) * 0.09853;

if ( batterieV < 1240 &&  batterieV > 800){
 mot1 += mot1 * ((1240 - batterieV)/(float)3500);
 mot2 += mot2 * ((1240 - batterieV)/(float)3500);
 mot3 += mot3 * ((1240 - batterieV)/(float)3500);
  mot4 += mot4 * ((1240 - batterieV)/(float)3500);
  }


if (mot1 < 1100) mot1 = 1050;
if (mot1 > 2000) mot1 = 2000;
if (mot2 < 1100) mot2 = 1050;
if (mot2 > 2000) mot2 = 2000;
if (mot3 < 1100) mot3 = 1050;
if (mot3 > 2000) mot3 = 2000;
if (mot4 < 1100) mot4 = 1050;
if (mot4 > 2000) mot4 = 2000;

} else{
mot1 = 1000;
mot2 = 1000;
mot3 = 1000;
mot4 = 1000;


}


}

void transmission(){



while (micros()-prevmicros < 4000);

prevmicros = micros();
PORTA |= B11110000;


while( PORTA >= 16){
prelmicros = micros();
if ( (mot1 + prevmicros) <= prelmicros) PORTA &= B11101111;
if ( (mot2 + prevmicros) <= prelmicros) PORTA &= B11011111;
if ( (mot3 + prevmicros) <= prelmicros) PORTA &= B10111111;
if ( (mot4 + prevmicros) <= prelmicros) PORTA &= B01111111;

}

}



void communication(){

Wire.beginTransmission(MPU_ADDRESS);
Wire.write(0x6B);
Wire.write(0x00);
Wire.endTransmission();


Wire.beginTransmission(MPU_ADDRESS);
Wire.write(0x1B);
Wire.write(0x08);
Wire.endTransmission();


Wire.beginTransmission(MPU_ADDRESS);
Wire.write(0x1C);
Wire.write(0x10);
Wire.endTransmission();

Wire.beginTransmission(MPU_ADDRESS);
Wire.write(0x1A);
Wire.write(0x03);
Wire.endTransmission();


 Wire.beginTransmission(MPU_ADDRESS1);
Wire.write(0x6B);
Wire.write(0x00);
Wire.endTransmission();


Wire.beginTransmission(MPU_ADDRESS1);
Wire.write(0x1B);
Wire.write(0x08);
Wire.endTransmission();


Wire.beginTransmission(MPU_ADDRESS1);
Wire.write(0x1C);
Wire.write(0x10);
Wire.endTransmission();

Wire.beginTransmission(MPU_ADDRESS1);
Wire.write(0x1A);
Wire.write(0x03);
Wire.endTransmission();

}



void Emoyen(){
  int max_samples = 2000;
for (int i = 0; i < max_samples; i++) {
  lectureMPU();
   Eroll1 += Rollgyro1;
  Epitch1 += Pitchgyro1;
  Eyaw1 += Yawgyro1;

  Eroll += Rollgyro;
  Epitch += Pitchgyro;
  Eyaw += Yawgyro;
  PORTA |= B11110000;
  delayMicroseconds(1000);
  PORTA &= B00001111;

  delay(3);
}
Eroll /= max_samples;
Epitch /= max_samples;
Eyaw /= max_samples;

Eroll1 /= max_samples;
Epitch1 /= max_samples;
Eyaw1 /= max_samples;


}


void lectureMPU (){

  Wire.beginTransmission(MPU_ADDRESS);
Wire.write(0x3B);
Wire.endTransmission();
Wire.requestFrom(MPU_ADDRESS, 14);


while (Wire.available() < 14);

Rollacc  = Wire.read() << 8 | Wire.read();
Pitchacc  = Wire.read() << 8 | Wire.read();
Yawacc  = Wire.read() << 8 | Wire.read();
temperature = Wire.read() << 8 | Wire.read();
Rollgyro = Wire.read() << 8 | Wire.read();
Pitchgyro = Wire.read() << 8 | Wire.read();
Yawgyro = Wire.read() << 8 | Wire.read();

 Wire.beginTransmission(MPU_ADDRESS1);
Wire.write(0x3B);
Wire.endTransmission();
Wire.requestFrom(MPU_ADDRESS1, 14);


while (Wire.available() < 14);

Rollacc1  = Wire.read() << 8 | Wire.read();
Pitchacc1  = Wire.read() << 8 | Wire.read();
Yawacc1  = Wire.read() << 8 | Wire.read();
temperature1 = Wire.read() << 8 | Wire.read();
Rollgyro1 = Wire.read() << 8 | Wire.read();
Pitchgyro1 = Wire.read() << 8 | Wire.read();
Yawgyro1 = Wire.read() << 8 | Wire.read();

}


void ANgyro() {

Rollgyro -= Eroll;
Pitchgyro -= Epitch;
Yawgyro -= Eyaw;

 Rollgyro1 -= Eroll1;
Pitchgyro1 -= Epitch1;
Yawgyro1 -= Eyaw1;



angleRO += (Rollgyro / (FREQ * SSF_GYRO));
anglePO += (-Pitchgyro / (FREQ * SSF_GYRO));
 angleRO1 += (Rollgyro1 / (FREQ * SSF_GYRO));
anglePO1 += (-Pitchgyro1 / (FREQ * SSF_GYRO));



anglePO += angleRO * sin(Yawgyro * (PI / (FREQ * SSF_GYRO * 180)));

angleRO -= anglePO * sin(Yawgyro * (PI / (FREQ * SSF_GYRO * 180)));

anglePO1 += angleRO1 * sin(Yawgyro1 * (PI / (FREQ * SSF_GYRO * 180)));

angleRO1 -= anglePO1 * sin(Yawgyro1 * (PI / (FREQ * SSF_GYRO * 180)));

}

void ANacc(){


    acc_total_vector = sqrt(pow(Rollacc, 2) + pow(Pitchacc, 2) + pow(Yawacc, 2));
    acc_total_vector1 = sqrt(pow(Rollacc1, 2) + pow(Pitchacc1, 2) + pow(Yawacc1, 2));


if (abs(Rollacc) < acc_total_vector) {
  RollaccA = asin((float)Pitchacc / acc_total_vector) * (180 / PI);
}

if (abs(Pitchacc) < acc_total_vector) {
  PitchaccA = asin((float)Rollacc / acc_total_vector) * (180 / PI);
}

 if (abs(Rollacc) < acc_total_vector) {
  RollaccA1 = asin((float)Pitchacc1 / acc_total_vector1) * (180 / PI);
}


}


void calculangle () {

if (initialized) {
  //  filtre plus le temps de bouclage est long (1-t)
  angleRO = angleRO * 0.996 + RollaccA * 0.004;//0.98  0.02
  angleRO1 = angleRO1 * 0.996 + RollaccA1* 0.004;
} else {
  // premiere mesure angle de l' acceleromettre
  angleRO = RollaccA;
  angleRO1 =  RollaccA1;
  initialized = true;
}


angleR  = angleR * 0.9 + angleRO * 0.1;
angleP = angleP * 0.9 + angleRO1 * 0.1;
ASR = (ASR * 0.7) + ((Rollgyro / 65.5) * 0.3);
ASP = (ASP * 0.7) + ((Rollgyro1 / 65.5) * 0.3);
ASY = (ASY * 0.7) + ((Yawgyro/ 65.5) * 0.3);

Serial.print("\n");
Serial.print(angleP);
}








ISR(PCINT0_vect)
{
  current_time = micros();

  // Channel 1 -------------------------------------------------
  if (PINB & B00000001) {
      if (previous_state[0] == LOW) {
          previous_state[0] = HIGH;
          timer[0]          = current_time;
      }
  } else if(previous_state[0] == HIGH) {
      previous_state[0] = LOW;
      pulse_duration[0] = current_time - timer[0];
  }

  // Channel 2 -------------------------------------------------
  if (PINB & B00000010) {
      if (previous_state[1] == LOW) {
          previous_state[1] = HIGH;
          timer[1]          = current_time;
      }
  } else if(previous_state[1] == HIGH) {
      previous_state[1] = LOW;
      pulse_duration[1] = current_time - timer[1];
  }

  // Channel 3 -------------------------------------------------
  if (PINB & B00010000) {
      if (previous_state[2] == LOW) {
          previous_state[2] = HIGH;
          timer[2]          = current_time;
      }
  } else if(previous_state[2] == HIGH) {
      previous_state[2] = LOW;
      pulse_duration[2] = current_time - timer[2];
  }

  // Channel 4 -------------------------------------------------
  if (PINB & B00001000) {
      if (previous_state[3] == LOW) {
          previous_state[3] = HIGH;
          timer[3]          = current_time;
      }
  } else if(previous_state[3] == HIGH) {
      previous_state[3] = LOW;
      pulse_duration[3] = current_time - timer[3];
  }

    if (PINB & B00100000) {
      if (previous_state[4] == LOW) {
          previous_state[4] = HIGH;
          timer[4]          = current_time;
      }
  } else if(previous_state[4] == HIGH) {
      previous_state[4] = LOW;
      pulse_duration[4] = current_time - timer[4];
  }

     if (PINB & B10000000) {
      if (previous_state[5] == LOW) {
          previous_state[5] = HIGH;
          timer[5]          = current_time;
      }
  } else if(previous_state[5] == HIGH) {
      previous_state[5] = LOW;
      pulse_duration[5] = current_time - timer[5];
  }
}

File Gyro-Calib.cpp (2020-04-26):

 #include "I2Cdev.h"
#include "MPU6050.h"
#include "Wire.h"

///////////////////////////////////   CONFIGURATION   /////////////////////////////
//Change this 3 variables if you want to fine tune the skecth to your needs.
int buffersize=1000;     //Amount of readings used to average, make it higher to get more precision but sketch will be slower  (default:1000)
int acel_deadzone=8;     //Acelerometer error allowed, make it lower to get more precision, but sketch may not converge  (default:8)
int giro_deadzone=1;     //Giro error allowed, make it lower to get more precision, but sketch may not converge  (default:1)

// default I2C address is 0x68
// specific I2C addresses may be passed as a parameter here
// AD0 low = 0x68 (default for InvenSense evaluation board)
// AD0 high = 0x69
//MPU6050 accelgyro;
MPU6050 accelgyro(0x69); // <-- use for AD0 high

int16_t ax, ay, az,gx, gy, gz;

int mean_ax,mean_ay,mean_az,mean_gx,mean_gy,mean_gz,state=0;
int ax_offset,ay_offset,az_offset,gx_offset,gy_offset,gz_offset;

///////////////////////////////////   SETUP   ////////////////////////////////////
void setup() {
  // join I2C bus (I2Cdev library doesn't do this automatically)
  Wire.begin();
  // COMMENT NEXT LINE IF YOU ARE USING ARDUINO DUE
  TWBR = 24; // 400kHz I2C clock (200kHz if CPU is 8MHz). Leonardo measured 250kHz.

  // initialize serial communication
  Serial.begin(115200);

  // initialize device
  accelgyro.initialize();

  // wait for ready
  while (Serial.available() && Serial.read()); // empty buffer
  while (!Serial.available()){
    Serial.println(F("Send any character to start sketch.\n"));
    delay(1500);
  }
  while (Serial.available() && Serial.read()); // empty buffer again

  // start message
  Serial.println("\nMPU6050 Calibration Sketch");
  delay(2000);
  Serial.println("\nYour MPU6050 should be placed in horizontal position, with package letters facing up. \nDon't touch it until you see a finish message.\n");
  delay(3000);
  // verify connection
  Serial.println(accelgyro.testConnection() ? "MPU6050 connection successful" : "MPU6050 connection failed");
  delay(1000);
  // reset offsets
  accelgyro.setXAccelOffset(0);
  accelgyro.setYAccelOffset(0);
  accelgyro.setZAccelOffset(0);
  accelgyro.setXGyroOffset(0);
  accelgyro.setYGyroOffset(0);
  accelgyro.setZGyroOffset(0);
}

///////////////////////////////////   LOOP   ////////////////////////////////////
void loop() {
  if (state==0){
    Serial.println("\nReading sensors for first time...");
    meansensors();
    state++;
    delay(1000);
  }

  if (state==1) {
    Serial.println("\nCalculating offsets...");
    calibration();
    state++;
    delay(1000);
  }

  if (state==2) {
    meansensors();
    Serial.println("\nFINISHED!");
    Serial.print("\nSensor readings with offsets:\t");
    Serial.print(mean_ax);
    Serial.print("\t");
    Serial.print(mean_ay);
    Serial.print("\t");
    Serial.print(mean_az);
    Serial.print("\t");
    Serial.print(mean_gx);
    Serial.print("\t");
    Serial.print(mean_gy);
    Serial.print("\t");
    Serial.println(mean_gz);
    Serial.print("Your offsets:\t");
    Serial.print(ax_offset);
    Serial.print("\t");
    Serial.print(ay_offset);
    Serial.print("\t");
    Serial.print(az_offset);
    Serial.print("\t");
    Serial.print(gx_offset);
    Serial.print("\t");
    Serial.print(gy_offset);
    Serial.print("\t");
    Serial.println(gz_offset);
    Serial.println("\nData is printed as: acelX acelY acelZ giroX giroY giroZ");
    Serial.println("Check that your sensor readings are close to 0 0 16384 0 0 0");
    Serial.println("If calibration was succesful write down your offsets so you can set them in your projects using something similar to mpu.setXAccelOffset(youroffset)");
    while (1);
  }
}

///////////////////////////////////   FUNCTIONS   ////////////////////////////////////
void meansensors(){
  long i=0,buff_ax=0,buff_ay=0,buff_az=0,buff_gx=0,buff_gy=0,buff_gz=0;

  while (i<(buffersize+101)){
    // read raw accel/gyro measurements from device
    accelgyro.getMotion6(&ax, &ay, &az, &gx, &gy, &gz);

    if (i>100 && i<=(buffersize+100)){ //First 100 measures are discarded
      buff_ax=buff_ax+ax;
      buff_ay=buff_ay+ay;
      buff_az=buff_az+az;
      buff_gx=buff_gx+gx;
      buff_gy=buff_gy+gy;
      buff_gz=buff_gz+gz;
    }
    if (i==(buffersize+100)){
      mean_ax=buff_ax/buffersize;
      mean_ay=buff_ay/buffersize;
      mean_az=buff_az/buffersize;
      mean_gx=buff_gx/buffersize;
      mean_gy=buff_gy/buffersize;
      mean_gz=buff_gz/buffersize;
    }
    i++;
    delay(2); //Needed so we don't get repeated measures
  }
}

void calibration(){
  ax_offset=-mean_ax/8;
  ay_offset=-mean_ay/8;
  az_offset=(16384-mean_az)/8;

  gx_offset=-mean_gx/4;
  gy_offset=-mean_gy/4;
  gz_offset=-mean_gz/4;
  while (1){
    int ready=0;
    accelgyro.setXAccelOffset(ax_offset);
    accelgyro.setYAccelOffset(ay_offset);
    accelgyro.setZAccelOffset(az_offset);

    accelgyro.setXGyroOffset(gx_offset);
    accelgyro.setYGyroOffset(gy_offset);
    accelgyro.setZGyroOffset(gz_offset);

    meansensors();
    Serial.println("...");

    if (abs(mean_ax)<=acel_deadzone) ready++;
    else ax_offset=ax_offset-mean_ax/acel_deadzone;

    if (abs(mean_ay)<=acel_deadzone) ready++;
    else ay_offset=ay_offset-mean_ay/acel_deadzone;

    if (abs(16384-mean_az)<=acel_deadzone) ready++;
    else az_offset=az_offset+(16384-mean_az)/acel_deadzone;

    if (abs(mean_gx)<=giro_deadzone) ready++;
    else gx_offset=gx_offset-mean_gx/(giro_deadzone+1);

    if (abs(mean_gy)<=giro_deadzone) ready++;
    else gy_offset=gy_offset-mean_gy/(giro_deadzone+1);

    if (abs(mean_gz)<=giro_deadzone) ready++;
    else gz_offset=gz_offset-mean_gz/(giro_deadzone+1);

    if (ready==6) break;
  }
}

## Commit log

2020-04-06 Update README.md
    Drone quadrimoteur en X.
    Frame imprimée en 3D.
    Controleur de vol (P.I.D): arduino Uno ou arduino mega.
2020-04-06 Fich stl
    [N.ruche.stl]
2020-04-24 Update
    Programme contrôleur de vol arduino uno un Gyro.
